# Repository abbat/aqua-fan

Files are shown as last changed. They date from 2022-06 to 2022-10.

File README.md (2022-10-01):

# aqua-fan

Проект кулера (вентиляторного охлаждения) для аквариума с крышкой. Позволяет понизить температуру воды в аквариуме на 4°C (±0.3°C) относительно комнатной, что актуально для помещений без кондиционера в летний период.

Изначально разрабатывался для аквариума [EHEIM vivalineLED 126](https://eheim.com/en_GB/aquatics/aquariums/aquariums-fresh-water/vivalineled/vivalineled-126), но это ограничение касается только модели корпуса для печати на 3D принтере (в программно-аппаратную же часть заложено масштабирование на различные конфигурации).

<p align='center'>
EHEIM vivaline aquarium fan cooler Вентиляторный кулер для аквариума EHEIM vivaline 126
EHEIM vivaline aquarium fan cooler Вентиляторный кулер для аквариума EHEIM vivaline 126
</p>

## Возможности

* Крепление на короб (крышку). Все коммерческие решения (например [GHL Aquarium Fans](https://www.aquariumcomputer.com/products/ghl-cooling-technology/aquarium-fans-propellerbreeze/), [Aqua Medic Arctic Breeze](https://www.aqua-medic.de/index.php?r=catalog/product&id=66&cid=34)) предполагают крепление блока вентиляторов клипсами на край стекла толщиной до 21 мм. Однако ширина короба аквариума данного типа 26 мм., что делает невозможным крепление на клипсы и потребовало бы открытия крышки (если бы крепление все же было возможно).
* Низкий уровень шума благодаря автоматической регулировке скорости вращения вентиляторов в зависимости от разницы температур (в отличии, например, от контроллеров [Aqua Medic Cool Control](https://www.aqua-medic.de/index.php?r=catalog/product&id=475&cid=34), у которых вентиляторы всегда работают на максимально разрешенной скорости).
* Контроль и подстройка скорости вращения по показаниям тахометров самих вентиляторов. Все коммерческие решения используют регулировку скорости вращения через изменение напряжения питания без использования обратной связи, а для различных моделей вентиляторов зависимость скорости вращения от напряжения может быть нелинейной (например см. спецификацию [be quiet! Pure Wings 2](https://www.bequiet.com/ru/casefans/505)) и разной даже для одной модели вентиляторов в блоке.

<p align='center'>
EHEIM vivaline aquarium fan cooler
EHEIM vivaline aquarium fan cooler
</p>

## Материалы

* [3D-модели](3d-model.md)
* [Аппаратное обеспечение](hardware.md)
* [Электрическая схема](schema.md)
* [Программное обеспечение](software.md)
* [Поддержка WiFi](wifi.md)

<p align='center'>
EHEIM vivaline aquarium fan cooler Вентиляторный кулер для аквариума с крышкой
EHEIM vivaline aquarium fan cooler Вентиляторный кулер для аквариума с крышкой
</p>

## Как можно помочь?

* Переведите этот документ или связанные материалы на свой родной язык;
* Исправляйте ошибки в этом документе или связанных материалах для своего родного языка;
* Делитесь информацией со своими друзьями;
* Отправляйте PR если вы имеете нестандартный аквариум под который не подходят коммерческие решения, разработчик, схемотехник или успешны в 3D моделировании и печати.

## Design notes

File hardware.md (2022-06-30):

# Аппаратное обеспечение

Все платы, датчики и расходники можно приобрести на AliExpress. Для упрощения поиска в описание добавлены ключевые слова и изображения.

ПО поддерживает от 1 до 3 вентиляторов с управлением скоростью вращения через `pwm` (4-pin). [Рекомендуется](fan-matrix.md) использовать вентиляторы `Noctua` - при хорошей производительности у них минимальный уровень шума (что особенно ценно в ночное время). Вообще, выбор хороших вентиляторов практически полностью определяет "удачность" конструкции - не экономьте на этом пункте.

<p align='center'>
Noctua NF-B9 redux-1600 PWM (92mm)
</p>

Так же, для уменьшения уровня шума, рекомендуется использовать силиконовые антивибрационные крепления, а для защиты лопастей вентиляторов - решетки. Для подключения вентиляторов используются коннекторы `KF2510-4AW`. Распайка коннекторов приведена в [схеме](schema.md), во время перепрограммирования плат(ы) вентиляторы должны отключаться от общей схемы!

<p align='center'>
Силиконовые крепления для вентиляторов
Металлические решетки для вентиляторов
4-pin коннкеторы KF2510-4AW для вентиляторов
</p>

В исходном проекте решетки крепятся силиконовыми креплениями непосредственно к вентиляторам, а сами вентиляторы удерживаются выступающей частью силиконовых креплений в специально отведенных внутренних пазах корпуса. Таким образом уменьшается передача вибрации от вентиляторов на корпус и далее на аквариум.

Для нестандартных вариантов крепления вентиляторов под крышкой могут помочь фиксирующие скобы ("пряжки") для объединения вентиляторов в блок, кронштейны для аквариумных светильников (например `NICREW`), поликарбонатные (акриловые) трубки (например `Uxcell`).

<p align='center'>
Фиксирующая скоба ("пряжка") для вентилятора
Кронштейны для аквариумных светильников NICREW
</p>

Контроллер вентиляторов работает на базе `Arduino Nano` или `Arduino Mini`. Рекомендуется `Arduino Nano`, т.к. для данной платы не потребуется дополнительно приобретать адаптер TTL (в случае его отсутствия). Так же подойдет любая другая плата `ATmega328` (`Arduino Uno`), но из за габаритов ее может не получится разместить в исходном корпусе.

При желании получения доступа по WiFi необходима дополнительная плата `Wi-Fi Wemos D1 Mini` (`ESP8266`). На практике данная возможность полезна только при активной разработке (перепрошивка через `OTA` без необходимости вскрытия корпуса и подключения к плате через USB). В обычной же жизни ("один раз настроил и забыл") эта возможность будет настолько редко востребованной, что усложнение схемы ради нее видится нецелесообразным.

В случае использования двух плат необходим блок питания на 5V. Для этих целей рекомендуется использовать `DC Power Shield for WEMOS D1 mini` (можно использовать любой другой блок питания, но с этим будет удобнее монтаж). В случае использования одноплатной схемы отдельный блок питания так же рекомендуется, но не является обязательным - `Arduino Nano` может быть напрямую запитана от 12V, а мощности ее внутреннего стабилизатора вполне достаточно для питания периферии.

<p align='center'>
Arduino Nano
Wi-Fi Wemos D1 Mini
DC Power Shield for WEMOS D1 mini
</p>

Питание в корпус подается через стандартный разъем 5.5 x 2.1 мм. от внешнего адаптера питания на 12V / 1A (одна плата) или 1.5А (две платы).

<p align='center'>
Разъем питания 5.5 x 2.1 мм.
Адаптер питания 12V / 2A (EU)
</p>

В качестве датчика температуры воды [рекомендуется](sensor-matrix.md) датчик `DS18B20` в пластиковом герметичном исполнении (ключевое слово для поиска `Taidacent DS18B20`).

<p align='center'>
Датчик температуры Taidacent DS18B20
Датчик температуры Sonoff DS18B20
</p>

Дополнительно для подключения датчика потребуются плата-адаптер с подтягивающим резистором, 4-pin разъем `PJ-392A` и 4-pin коннектор 3.5 мм. Разъем и коннектор опциональны, но с ними удобно отключать датчик при обслуживании. Распайка коннектора, совместимая с датчиками `Sonoff`, приведена в [схеме](schema.md).

<p align='center'>
Адаптер для подключения датчика температуры DS18B20
4-pin аудио разъем 3.5 мм.
4-pin аудио коннкетор 3.5 мм.
</p>

Дисплей `SSD1306 128x64` с интерфейсом IIC / I2C (4 pin, не путать с интерфейсом SPI - 7 pin). Данные дисплеи представлены в разных цветах (в том числе и с поддержкой двух цветов), рекомендуется использовать одноцветный голубой (не такой яркий ночью как желтый или белый). Наличие дисплея является опциональным, все необходимые параметры для работы ПО можно задать на этапе компиляции в файле конфигурации `config.h`.

<p align='center'>
Дисплей SSD1306 128x64 IIC/I2C
</p>

Сенсорные кнопки `TTP223` для конфигурирования температуры, ограничения мощности вентиляторов и других настроек. Кнопки имеют смысл только при наличии дисплея (т.е. так же являются опциональными). Сенсорные кнопки при отличной чувствительности через пластиковый корпус оказались и удобнее и дешевле механических.

<p align='center'>
Сенсорные кнопки TTP223
</p>

Зуммер ("пищалка") `KY-012` (активный, однотонный) или `KY-006` (пассивный, мелодии) - может использоваться для звуковой индикации ошибок или оповещения о событиях (ошибка вентиляторов, критическое повышение температуры и т.д.). На данный момент поддержка зуммеров не реализована в ПО, однако можно подключить пассивный зуммер с учетом возможных будущих доработок.

<p align='center'>
Зуммер ("пищалка") KY-012
Зуммер ("пищалка") KY-006
</p>

Для монтажа всех компонентов в корпусе потребуются провода типа `Dupont` (разноцветные), термоусадочные трубки (маленькие с учетом диаметра проводов), паяльник (припой, флюс), мультиметр, горячий клеевой пистолет, и прочие инструменты (кусачки, пинцет). Если вы не занимаетесь схемотехникой, то приобретать все это для разовой задачи не имеет смысла - для пайки десятка проводов будет дешевле обратиться к специалисту или в любой сервисный центр по ремонту техники.

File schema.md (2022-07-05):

# Электрическая схема

Контроллер может быть собран по двум схемам:

* На базе одной платы `Arduino Nano` (без поддержки WiFi)
* На базе двух плат `Arduino Nano` и `Wi-Fi Wemos D1 Mini` (с поддержкой WiFi)

Поддержка WiFi полезна только при активной разработке (перепрошивка через `OTA` без необходимости вскрытия корпуса и подключения к плате через USB). В обычной же жизни ("один раз настроил и забыл") эта возможность будет настолько редко востребованной, что усложнение схемы ради нее видится нецелесообразным.

Обе схемы отображают подключение коннекторов для 3-х вентиляторов. В случае использования меньшего количества вентиляторов можно просто убирать из схемы неиспользуемые (начиная с 3-го).

Обе схемы отображают подключение двух датчиков температуры воды:

* `DS18B20` (через адаптер и аудио-коннектор 3.5 мм.);
* Инфракрасный `GY-906` (`MLX90614`).

ПО может работать как с обоими датчиками одновременно, так и с любым из них. [Практические испытания](sensor-matrix.md) показали, что датчик `GY-906` достаточно сильно "шумит" из за внешних воздействий и, если вам не требуется дополнительный контроль по второму датчику, его можно исключить из схемы. Так же, если будет сделан выбор в пользу ИК-датчика `GY-906` (и неприемлемости погружения в воду `DS18B20` например, из соображений эстетики), можно исключить из схемы аудио-гнездо 3.5 mm и адаптер `DS18B20`.

Помимо датчика `GY-906` по шине I2C можно подключить любые дополнительные датчики по вашему усмотрению аналогично подключению `GY-906` (на данный момент эта возможность носит экспериментальный характер).

Дисплей `SSD1306 128x64` и сенсорные кнопки `TTP223` являются опциональными - все параметры ПО можно задать на этапе компиляции. Если вам не требуется визуальное отображение информации или не требуется изменение настроек (конфигурирования температуры, ограничения мощности вентиляторов и т.д.), то дисплей и / или кнопки можно исключить из схемы.

Обе схемы отображают подключение зуммера ("пищалки") `KY-006` для звуковой сигнализации о различных событиях (ошибка вентиляторов, критическое повышение температуры и т.д.). На данный момент ПО не поддерживает эту возможность, однако не исключена поддержка в будущем. Зуммер так же можно исключить из схемы.

Крепление плат в [корпусе](3d-model.md) производится на термоклей (поскольку отпечатать на 3D-принтере ровные аккуратные крепления не представляется возможным), монтаж навесной проводами типа `dupont` (для цветовой маркировки и / или возможности размыкания узлов). В случае необходимости демонтажа для термоклея можно использовать изопропиловый спирт.

## Схема 1

Схема с одной платой без поддержки WiFi.

<p align='center'>
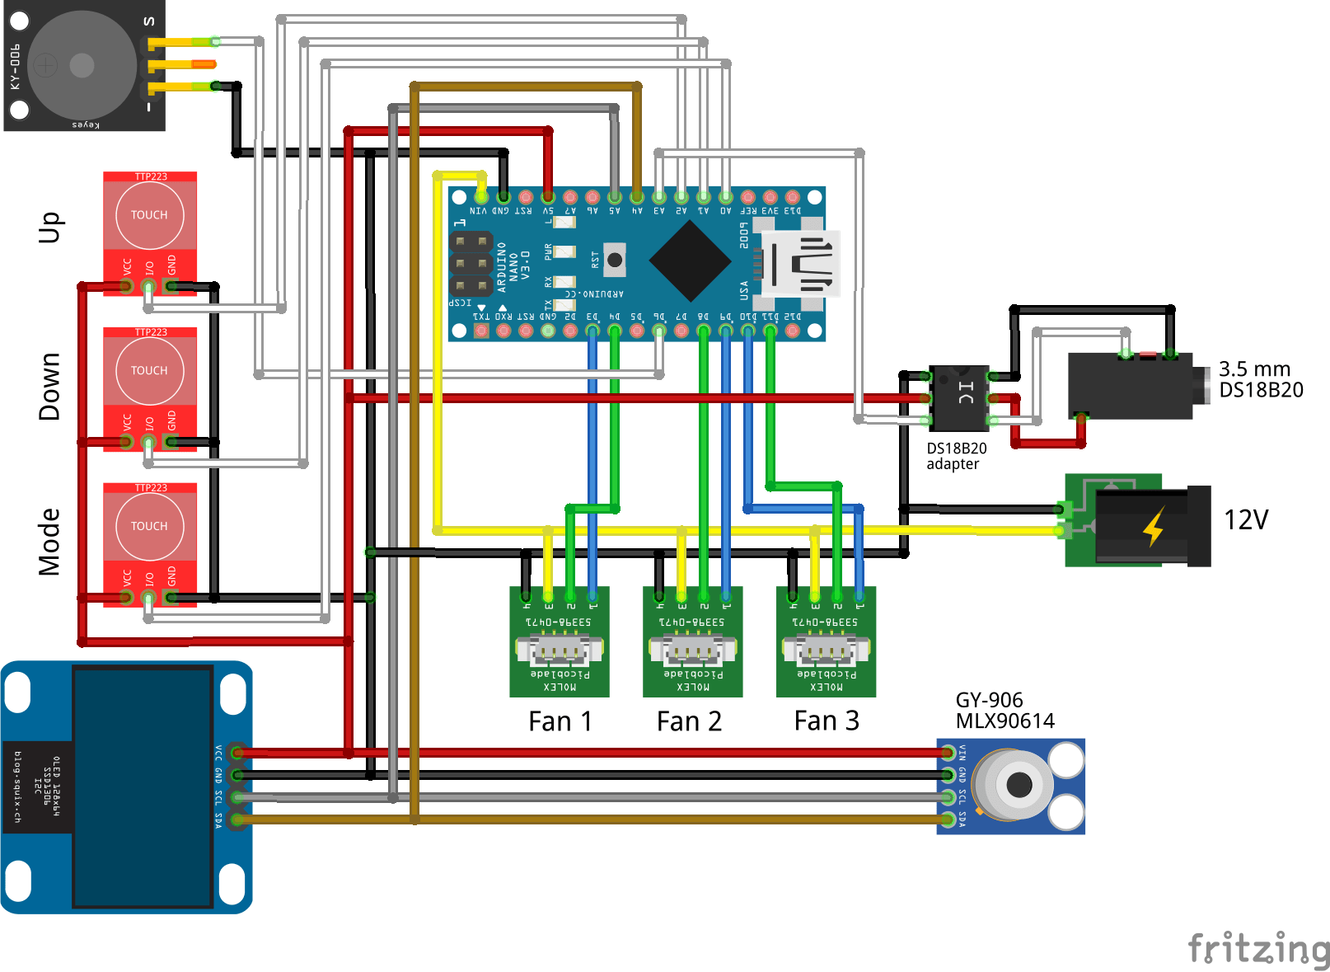
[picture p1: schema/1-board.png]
Одноплатная схема кулера для аквариума

</p>

## Схема 2

Схема с двумя платами и поддержкой WiFi.

<p align='center'>
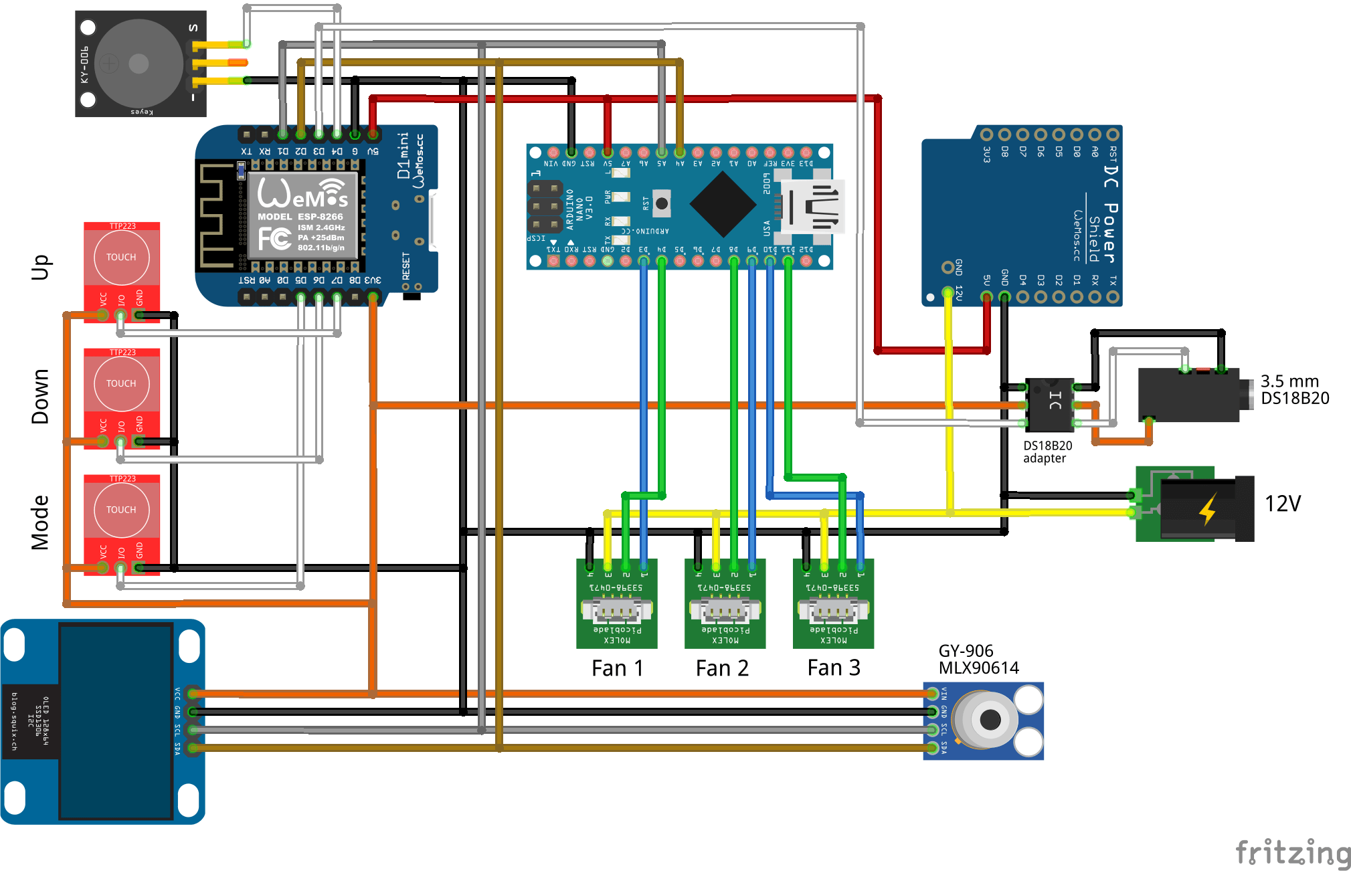
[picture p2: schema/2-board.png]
Схема кулера для аквариума с поддержкой WiFi

</p>

## Прочее

### DS18B20

При использовании датчика `DS18B20` аудио-штекер 3.5 мм. рекомендуется распаивать совместимым с датчиком `Sonoff` (который поставляется с уже распаяным штекером).

<p align='center'>
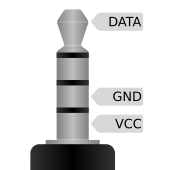
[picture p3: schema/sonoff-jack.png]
Распайка штекера Sonoff DS18B20

</p>

* `DATA` - данные (белый)
* `GND` - земля (черный)
* `VCC` - питание (красный +5V, оранжевый +3V, у датчика `Taidacent` - розовый)

При монтаже гнездо и штекер имеет смысл прозвонить мультиметром на соответствие контактов.

### KF2510-4AW

Штекер `KF2510-4AW` имеет ключ для корректного подключения вентилятора. Распайка штекера и гнезда приведена ниже:

<p align='center'>
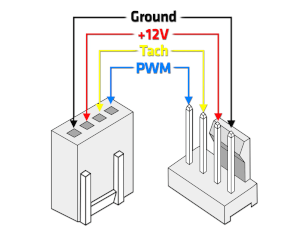
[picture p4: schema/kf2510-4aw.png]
Распайка штекера KF2510-4AW.png Распайка штекера KF2510-4AW

</p>

* `Ground` - земля (черный)
* `+12V` - питание (на схеме желтый)
* `Tach` - показания тахометра (на схеме зеленый)
* `PWM` - управление скоростью вращения (голубой)

## Как можно помочь?

Схемы созданы с использованием [fritzing.app](https://github.com/fritzing/fritzing-app), исходники лежат в директории `schema` проекта:

* [1-board.fzz](schema/1-board.fzz) - схема 1 (одна плата)
* [2-board.fzz](schema/2-board.fzz) - схема 2 (две платы)

Поскольку я делал это первый раз в жизни (как и держал пяльник), буду рад вашим PR с улчшениями.

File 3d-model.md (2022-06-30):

# 3D-модели

На текущий момент в проекте присутствует только одна модель корпуса для печати на 3D-принтере.

## EHEIM vivalineLED 126

### 3 x 92 мм. вентиляторы

<p align='center'>
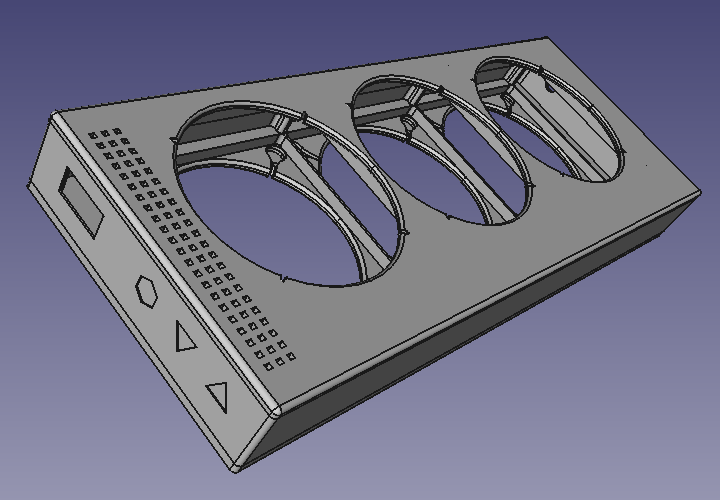
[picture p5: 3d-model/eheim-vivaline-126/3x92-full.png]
3D модель корпуса для EHEIM vivalineLED 126 и 3 x 92 мм. вентиляторов

</p>

Исходники модели в формате `FreeCAD` лежат в директории `3d-model/eheim-vivaline-126` проекта ([3x92-full.FCStd.xz](3d-model/eheim-vivaline-126/3x92-full.FCStd.xz)). Там же находятся готовые к печати `stl` файлы:

* [3x92-bottom.stl.xz](3d-model/eheim-vivaline-126/3x92-bottom.stl.xz) - низ корпуса, подоходит для всех вариантов верха;
* [3x92-top-power.stl.xz](3d-model/eheim-vivaline-126/3x92-top-power.stl.xz) - верх корпуса с единственным отверстием под гнездо питания, может использоваться если у вас уже есть внешний контроллер и не хватает только блока вентиляторов;
* [3x92-top-ds18b20.stl.xz](3d-model/eheim-vivaline-126/3x92-top-ds18b20.stl.xz) - верх корпуса с отверстием под аудио-гнездо 3.5 мм. датчика `DS18B20`, может использоваться если вам не требуется индикация параметров работы на дисплее;
* [3x92-top-display.stl.xz](3d-model/eheim-vivaline-126/3x92-top-display.stl.xz) - верх корпуса с дисплеем, может использоваться если вам нужна индикация работы, но не требуется настройка парамеров;
* [3x92-top-buttons.stl.xz](3d-model/eheim-vivaline-126/3x92-top-buttons.stl.xz) - верх корпуса с кнопками, наиболее полный вариант.

Объем модели (`FreeCAD.ActiveDocument.ActiveObject.Shape.Volume / 1000`) составляет приблизительно 305 см³. Отпечатана в типографии [replica-3d.ru](https://replica-3d.ru) без склеек.

## Как можно помочь?

Буду рад вашим PR с новыми моделями корпусов под другие типы аквариумов или количество вентиляторов.

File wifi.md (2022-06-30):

# Поддержка WiFi

На данный момент ПО поддерживает минимальный набор JSON-API. Запросы делаются по протоколу http.

## Получение статуса

**Запрос**:

`GET /status`

**Ответ**:

`HTTP-200` и JSON, или код ошибки с описанием.

```
{
   "uptime" : 274043,               # время в секундах с момента загрузки контроллера
   "fans" : {
      "speed" : 23.7456446,         # текущая скорость вентиляторов в процентах (усредненная)
      "uptime" : 64031,             # время в секундах с момента запуска вентиляторов
      "items" : [                   # статистика по каждому из вентиляторов
         {
            "hirpm" : 1896,         # максимальный rpm вентилятора
            "rpm" : 449,            # текущий rpm вентилятора
            "speed" : 23.6814346,   # текущая скорость вентилятора в процентах
            "base" : 454,           # требуемый rpm вентилятора от системы управления
            "lopwm" : 13,           # значение скважности pwm ниже которого вентилятор останавливается (0 - 255)
            "hipwm" : 23,           # значение скважности pwm выше которого вентилятор запускается (0 - 255)
            "pwm" : 56              # текущее значение скважности pwm (0 - 255)
         },
         ...
      ]
   },
   "sensors" : [                     # статистика по каждому из сенсоров
      {
         "filtered" : 24.38318063,   # текущее сглаженное значение температуры
         "value" : 24.35790526,      # текущее "сырое" значение температуры
         "type" : "water",           # датчик измерения температуры воды
         "role" : "secondary",       # роль датчика (вторичный)
         "unit" : "C",               # единица измерения (°C)
         "sensor" : "MLX90614"       # наименование датчика
      },
      {
         "value" : 27.74999428,
         "role" : "primary",         # роль датчика (первичный)
         "unit" : "C",
         "type" : "ambient",         # датчик измерения температуры воздуха
         "sensor" : "MLX90614"
      },
      ...
   ],
   "ips" : [                         # список IP адресов платы
      "192.168.1.XXX",
      "2a02:2168:XXXX:XXXX:XXXX:XXXX:XXXX:XXXX"
   ],
   "ts" : "2022-06-30T22:04:29Z"     # текущее время (UTC)
}
```

## Установка параметра

**Запрос**:

`POST /set`

**Параметры**:

* `water-temperature-base` - требуемое значение температуры в °C;
* `min-fan-speed` - минимальная скорость вентиляторов в процентах (0 - 100, не может быть больше `max-fan-speed`);
* `max-fan-speed` - максимальная скорость вентиляторов в процентах (0 - 100, не может быть меньше `min-fan-speed`);

**Ответ**:

`HTTP-200`, или код ошибки с описанием.

## Как можно помочь?

Буду рад вашим PR с расширением JSON-API и созданию полноценного веб-интерфейса управления.

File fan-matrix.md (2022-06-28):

# Выбор вентиляторов

Модель (производитель) вентиляторов выбирались исходя из [обзора](https://www.overclockers.ua/cooler/arctic-bequiet-enermax-noctua-thermalright-xigmatek-zalman-120mm/all/). Критерий - максимальная производительность при минимуме шума (~20dB/A - это уже достаточно шумно). Кандидаты:

* [Noctua](https://noctua.at/en/products/fan);
* [be quiet!](https://www.bequiet.com/en/casefans).

Ограничения по габаритам:

* Глубина корпуса: 318.2 мм. (для [EHEIM vivalineLED 126](https://eheim.com/en_GB/aquatics/aquariums/aquariums-fresh-water/vivalineled/vivalineled-126));
* Перегородка между вентиляторами: 1.2 мм. (стандартный диаметр сопла 3D-принтера составляет 0.4 мм., а толщина стенки рекомендуется минимум в 3 раза больше).

Прочие ограничения:

* Питание 12V (можно 5V, но они обычно более шумные);
* Одна плата arduino nano может управлять тремя pwm вентиляторами.

Сводная таблица представлена ниже, исключены заведомо проигрышные варианты по шуму или производительности, указана минимальная цена в рублях на момент написания (текущие цены могут существенно отличаться).

```
+------------------------+---------+------+------+-------+-------+
|          name          |  size   | rpm  | dB/A | m³/h  | price |
+------------------------+---------+------+------+-------+-------+
| NF-P14s redux-1200 PWM | 2 x 140 | 1200 | 19.6 | 220.6 |  2906 |
| NF-S12A PWM            | 2 x 120 | 1200 | 17.8 | 215.0 |  3260 |
| NF-S12B redux-1200 PWM | 2 x 120 | 1200 | 18.1 | 201.2 |  2396 |
| NF-B9 redux-1600 PWM   | 3 x  92 | 1600 | 17.6 | 192.9 |  2751 |
+------------------------+---------+------+------+-------+-------+
| Silent Wings 3-140     | 2 x 140 | 1000 | 15.5 | 202.2 |  3462 |
| Silent Wings 3-120     | 2 x 120 | 1450 | 16.4 | 171.6 |  3196 |
+------------------------+---------+------+------+-------+-------+
| Pure Wings 2-140       | 2 x 140 | 1000 | 18.8 | 208.0 |  1578 |
| Pure Wings 2-92        | 3 x  92 | 1900 | 19.6 | 168.0 |  1920 |
+------------------------+---------+------+------+-------+-------+
```

Особенностью вентиляторов `be quiet!` серии `Pure Wings` является то, что они [не останавливаются](https://www.bequiet.com/ru/casefans/618) при нулевой скважности pwm - т.е. регулирование скорости вращения возможно только по питанию и в [ограниченном диапазоне скоростей](https://www.bequiet.com/ru/casefans/505).

Итоговый выбор сводится к вариантам на базе `Noctua`:

* 2 x `NF-S12A PWM` / `NF-S12B redux-1200 PWM` - по 37.3 мм спереди и сзади по глубине под гнезда и дисплей;
* 3 x `NF-B9 redux-1600 PWM` - по 18.7 мм спереди и сзади по глубине под гнезда и дисплей.

Достоинства и недостатки 2-х вентиляторной схемы:

* `+` на 4 провода меньше;
* `+` больше пространства спереди и сзади под гнезда и платы;
* `-` корпус шире на 28 mm (возможно за счет перекомпановки это можно нивелировать);
* `-` меньше возможности по регулированию rpm на малых оборотах (когда часть вентиляторов может быть вообще выключена), но целесообразность этой возможности сомнительна.

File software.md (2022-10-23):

# Программное обеспечение

Исходный код находится в директории `src` проекта. Для сборки используется среда [Arduino IDE](https://www.arduino.cc/en/software) со следующими дополнительными библиотеками:

* [SoftTimers](https://github.com/end2endzone/SoftTimers);
* [GyverOLED](https://github.com/GyverLibs/GyverOLED);
* [GyverPWM](https://github.com/GyverLibs/GyverPWM);
* [EnableInterrupt](https://github.com/GreyGnome/EnableInterrupt).

Для работы с датчиками температуры используются следующие библиотеки:

* [OneWire](https://www.pjrc.com/teensy/td_libs_OneWire.html) - `DS18B20`;
* [DallasTemperature](https://github.com/milesburton/Arduino-Temperature-Control-Library) - `DS18B20`;
* [Adafruit-MLX90614-Library](https://github.com/adafruit/Adafruit-MLX90614-Library) - `GY-906` (`MLX90614ESF`).

Для работы в [схеме с двумя платами](schema.md) и поддержкой WiFi используются следующие библиотеки:

* [ESP8266 Arduino](https://arduino-esp8266.readthedocs.io/en/latest/);
* [ArduinoJSON](https://arduinojson.org/v6/api/).

Для работы с внешними (экспериментальными) датчиками используются следующие библиотеки:

* [Adafruit BME280 Library](https://github.com/adafruit/Adafruit_BME280_Library) - `BME280`;
* [arduino-sht](https://github.com/Sensirion/arduino-sht) - `SHT-3X` (`SHT-30`, `SHT-31`, `SHT-35`, `SHT-85`);
* [BH1750](https://github.com/claws/BH1750) - `BH1750`.

Все эти библиотеки могут быть установлены через менеджер библиотек `Arduino IDE`.

## Конфигурация

Конфигурация ПО задается в файле [config.h](src/config.h) через `#define` опции:

* `DISPLAY_TYPE` - тип дисплея:
  * (не задано) - система собирается и работает без поддержки дисплея и кнопок;
  * `DISPLAY_SSD1306_128_64` - поддержка дисплея `SSD1306 128x64` (включено по умолчанию в `config.h`).
* `PRIMARY_WATER_TEMPERATURE_SENSOR` - тип первичного (основного) датчика температуры воды:
  * `WATER_TEMPERATURE_SENSOR_DS18B20` - `DS18B20` (включено по умолчанию в `config.h`);
  * `WATER_TEMPERATURE_SENSOR_MLX90614` - `GY-906` (`MLX90614ESF`).
* `SECONDARY_WATER_TEMPERATURE_SENSOR` - типы вторичного (дополнительного) датчика температуры воды:
  * (не задано) - вторичный датчик отсутствует (по умолчанию);
  * остальные возможные значения такие же как у `PRIMARY_WATER_TEMPERATURE_SENSOR`.
* `ENABLE_WIFI` - включение [схемы с поддержкой WiFi](schema.md) (по умолчанию не задано):
  * `WIFI_SSID` - имя `SSID` для подключения к WiFi сети (по умолчанию не задано);
  * `WIFI_PASSWORD` - пароль для подключения к WiFi сети (по умолчанию не задано).

Экспериментальные опции:

* `EXTERNAL_SENSOR_0`, `EXTERNAL_SENSOR_1`, `EXTERNAL_SENSOR_2` - внешние сенсоры (по умолчанию не заданы):
  * `EXTERNAL_SENSOR_BME280` - датчик `BME280` (температура, влажность, давление);
  * `EXTERNAL_SENSOR_SHT3X` - датчик `SHT-3X` (температура, влажность).

### Контроллер

Значения ниже не используются, если они были сконфигурированы и сохранены в `EEPROM` (кнопками).

* `DEFAULT_WATER_TEMPERATURE_BASE` - базовая температура воды для поддержания в °C (по умолчанию 25);
* `DEFAULT_MIN_FAN_SPEED` - минимально разрешенная скорость вентиляторов в процентах (по умолчанию 0);
* `DEFAULT_MAX_FAN_SPEED` - максимально разрешенная скорость вентиляторов в процентах (по умолчанию 80).

Значения ниже не рекомендуются к изменению:

* `FAN_SPEED_TEMPERATURE_WINDOW` - ширина окна температур в °C в котором скорость вентиляторов меняется от 0 до 100% (по умолчанию 0.5);
* `WATER_TEMPERATURE_SENSOR_NOISE` - шум датчика в °C (по умолчанию 0.1 для `DS18B20` и 0.3 для `MLX90614`);
* `WATER_TEMPERATURE_SENSOR_NOISE_UPPER` - шум датчика в °C в сторону завышения показаний температуры (по умолчанию `WATER_TEMPERATURE_SENSOR_NOISE`);
* `WATER_TEMPERATURE_SENSOR_NOISE_LOWER` - шум датчика в °C в сторону занижения показаний температуры (по умолчанию `WATER_TEMPERATURE_SENSOR_NOISE`);
* `FAN_SPEED_NOISE_MULTIPLER` - основание логарифма для модели изменения скорости вращения вентиляторов (по умолчанию не задано - используется линейная модель, эквивалентная `FAN_SPEED_NOISE_MULTIPLER = 1`). Динамика изменения скорости вращения вентиляторов в зависимости от значения и разницы температур изображена на диаграме ниже. Значения более единицы подходят для очень тихих вентиляторов и удержания температуры в узком диапазоне. Значения менее единицы могут использоваться для шумных вентиляторов, но тогда придется пожертвовать диапазоном регулирования. На экспериментальном стенде стандартная линейная модель показала себя вполне адекватно и установка данной переменной в обычных условиях не требуется.

<p align='center'>
Зависимость изменения скорости работы вентиляторов от разницы температуры и FAN_SPEED_NOISE_MULTIPLER
</p>

* `FAN_SPEED_NOISE_HUMIDITY` - динамическое определение значения `FAN_SPEED_NOISE_MULTIPLER` в зависимости от влажности воздуха (по умолчанию не задано), где 100% влажности соответствует значению основания 10, и основанию 0.1 при влажности менее 1%. При задании опции `FAN_SPEED_NOISE_HUMIDITY` значение опции `FAN_SPEED_NOISE_MULTIPLER` игнорируется. Для работы требуется дополнительный датчик с поддержкой измерения влажности воздуха.

Алгоритм управления вентиляторами:

* Вентиляторы стартуют, если температура повысилась до значения `DEFAULT_WATER_TEMPERATURE_BASE` + `WATER_TEMPERATURE_SENSOR_NOISE_UPPER`;
* Вентиляторы останавливаются, если температура понизилась до значения `DEFAULT_WATER_TEMPERATURE_BASE` - `WATER_TEMPERATURE_SENSOR_NOISE_LOWER`;
* Вентиляторы работают на 100% мощности при превышении температуры `DEFAULT_WATER_TEMPERATURE_BASE` + `FAN_SPEED_TEMPERATURE_WINDOW`;
* Вентиляторы меняют скорость работы от 0 до 100% в диапазоне температур остановки и максимальной мощности.

### Датчики

**Общие параметры**

Значения ниже не рекомендуются к изменению:

* `FAST_SENSOR_UPDATE_INTERVAL` - время обновления показаний для "быстрых" датчиков в ms (по умолчанию 1000 = 1s);
* `STANDARD_SENSOR_UPDATE_INTERVAL` - время обновления показаний для "стандартных" датчиков в ms (по умолчанию 3000 = 3s);
* `SLOW_SENSOR_UPDATE_INTERVAL` - время обновления показаний для "медленных" датчиков в ms (по умолчанию 15000 = 15s).

**DS18B20**

* `ONE_WIRE_PIN` - номер `OneWire` пина для датчика (значение по умолчанию зависит от типа [схемы](schema.md), нельзя использовать пины D0 и D8 для платы `ESP8266`);
* `DS18B20_WATER_TEMPERATURE_SENSOR_INDEX` - индекс датчика (по умолчанию 0);
* `DS18B20_WATER_TEMPERATURE_SHIFT` - поправка датчика в °C (по умолчанию 0).

Значения ниже не рекомендуются к изменению:

* `DS18B20_WATER_TEMPERATURE_FILTER` - коэффициент IIR фильтра (по умолчанию 22, что соответствует ~5 минутам для стабилизации показаний при интервале обновления раз в 3s значения `STANDARD_SENSOR_UPDATE_INTERVAL`).

**MLX90614**

* `MLX90614_WATER_TEMPERATURE_SHIFT` - поправка датчика температуры объекта в °C (по умолчанию 0);
* `MLX90614_AMBIENT_TEMPERATURE_SHIFT` - поправка датчика температуры окружающего воздуха в °C (по умолчанию 0).

Значения ниже не рекомендуются к изменению:

* `MLX90614_WATER_TEMPERATURE_FILTER` - коэффициент IIR фильтра (по умолчанию 65 что соответствует ~5 минутам для стабилизации показаний при интервале обновления раз в 1s значения `FAST_SENSOR_UPDATE_INTERVAL`);
* `MLX90614_WATER_TEMPERATURE_MAX_FAILS` - максимальное число попыток измерения температуры объекта, прежде чем датчик будет переведен в режим ошибки (по умолчанию `MLX90614_AMBIENT_TEMPERATURE_MAX_FAILS`);
* `MLX90614_AMBIENT_TEMPERATURE_MAX_FAILS` - максимальное число попыток измерения температуры окружающего воздуха, прежде чем датчик будет переведен в режим ошибки (по умолчанию 60000 / `FAST_SENSOR_UPDATE_INTERVAL` = 60 попыток или 1 минута).

**BME280**

* `BME280_AMBIENT_TEMPERATURE_SHIFT` - поправка датчика температуры окружающего воздуха в °C (по умолчанию 0);
* `BME280_HUMIDITY_SHIFT` - поправка датчика влажности окружающего воздуха в % (по умолчанию 0);
* `BME280_PRESSURE_SHIFT` - поправка датчика давления окружающего воздуха в Па (по умолчанию 0).

**SHT-3X**

* `SHT3X_AMBIENT_TEMPERATURE_SHIFT` - поправка датчика температуры окружающего воздуха в °C (по умолчанию 0);
* `SHT3X_HUMIDITY_SHIFT` - поправка датчика влажности окружающего воздуха в % (по умолчанию 0).

**BH1750**

* `BH1750_LIGHT_SHIFT` - поправка датчика освещения в Lx (по умолчанию 0).

### Вентиляторы

* `FAN_COUNT` - количество вентиляторов (от 1 до 3, по умолчанию 3).

Значения ниже не рекомендуются к изменению:

* `FAN0_TAC` - номер пина tac (тахометр) для 1-го вентилятора (по умолчанию 4);
* `FAN1_TAC` - номер пина tac (тахометр) для 2-го вентилятора (по умолчанию 8);
* `FAN2_TAC` - номер пина tac (тахометр) для 3-го вентилятора (по умолчанию 11);
* `FAN_PWM_FREQ` - несущая частота pwm, Hz (по умолчанию 25000 = 25kHz);
* `FAN_UPDATE_INTERVAL` - интервал снятия показаний тахометра в ms (по умолчанию 2000 = 2s);
* `FAN_I2C_ADDRESS` - I2C адрес slave платы управления вентиляторами в схеме с двумя платами.

Из за особенностей генерации pwm, номера pwm-пинов жестко фиксированы на 3, 9 и 10.

### Дисплей

Дисплей неактивен, если не задан `DISPLAY_TYPE`.

* `DISPLAY_ADDRESS` - I2C адрес дисплея (по умолчанию `0x3C`).

Значения ниже не рекомендуются к изменению:

* `DISPLAY_UPDATE_INTERVAL` - время обновления информации на дисплее в ms (по умолчанию 1000 = 1s).

### Кнопки

Кнопки неактивны, если не задан `DISPLAY_TYPE`.

* `BUTTON_MODE_PIN` - номер пина для кнопки выбора режима (значение по умолчанию зависит от типа [схемы](schema.md));
* `BUTTON_DOWN_PIN` - номер пина для кнопки "вниз" (значение по умолчанию зависит от типа [схемы](schema.md));
* `BUTTON_UP_PIN` - номер пина для кнопки "вверх" (значение по умолчанию зависит от типа [схемы](schema.md)).

## Сборка

* Перед загрузкой ПО на плату отключите вентиляторы из схемы;
* Соедините нужную плату с компьютером через USB;
* Откройте проект в `Arduino IDE` и выберете нужный тип платы;
* Скомпилируйте и загрузите проект.

В случае использования двух плат рекомендуемые параметры сборки для `Wi-Fi Wemos D1 Mini`:

<p align='center'>
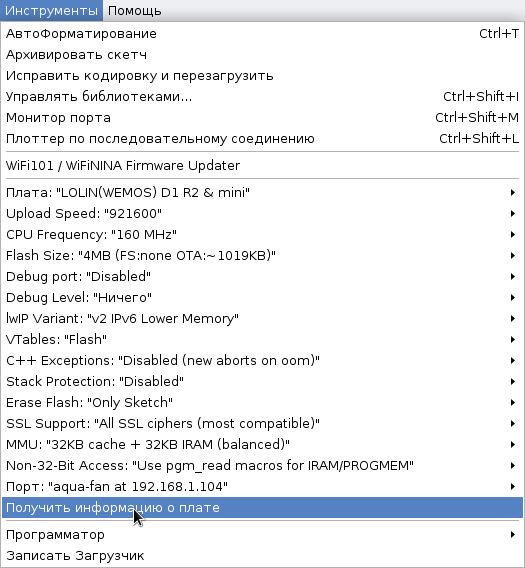
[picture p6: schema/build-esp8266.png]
Рекомендуемые параметры сборки для Wi-Fi Wemos D1 Mini

</p>

После первичной прошивки в дальнейшем можно использовать прошиву через `OTA` (по WiFi). Для этого может потребоваться разрешить на firewall компьютера трафик для `mDNS` и `OTA`. В терминах `iptables`:

```
# allow mdns
-A INPUT -d 224.0.0.251/32 -p udp -m udp --dport 5353 -j ACCEPT

# allow ota
-A INPUT -s 192.168.1.XXX/32 -p udp -j ACCEPT
-A INPUT -s 192.168.1.XXX/32 -p tcp -j ACCEPT
```

где `192.168.1.XXX` - адрес, назначенный WiFi плате.

## Как можно помочь?

Буду раз вашим PR с новыми функциями и исправлением ошибок.

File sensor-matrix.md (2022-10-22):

# Выбор датчиков

Критерий - удержание температуры воды без резких перепадов (например, 24°C ± 1°C в час). При этом по низкой стороне должен включаться обогреватель удерживающий температуру в нижнем диапазоне, а по высокой вентиляторы уже должны работать на 100% удерживая температуру в верхнем диапазоне. Поскольку одновременная работа обогревателя и вентиляторов является нецелесообразной, необходим диапазон температур, когда вентиляторы уже отключились, но нагреватель еще не включился и в обратную сторону. Поскольку большинство современных обогревателей (например, [EHEIM thermocontrol](https://eheim.com/en_GB/aquatics/technology/aquarium-heaters/thermocontrol-e/thermocontrol-e-100)) имеет точность ±0.5°C, то оптимальным режимом работы датчика будет 25°C ± 0.5°C.

Датчики с внешним креплением на стекло не рассматриваются по причине того, что при большой разнице температур (например, летом) им требуется хорошая теплоизоляция от внешней среды - корпус получится достаточно громоздким и не эстетичным.

Аналоговые датчики не рассматриваются по причине того, что в большинстве случаев они имеют более высокую погрешность и требуют самостоятельной упаковки в водонепроницаемую гильзу (т.е. дополнительный "колхоз").

Т.о. на рынке представлено по сути только два датчика для измерения температуры воды:

* `DS18B20` - погрешность ±0.5°C, разрешение 0.5°C - 0.0625°C (9-12 bit);
* `GY-906` (`MLX90614ESF-XXX`), разрешение 0.02°C:
  * `BAA` - погрешность ±0.5°C (single zone, 90° FOV);
  * `BCC` - погрешность ±0.5°C (gradient compensated, 35° FOV);
  * `DCI` - погрешность ±0.2°C (gradient compensated, 5° FOV).

## GY-906

Огромным достоинством датчика `GY-906` является то, что он не требует погружения в воду и может быть смонтирован прямо в корпусе с вентиляторами. Однако, точность показаний данного датчика очень сильно зависит от градиентов температур (подробности см. ["Thermal/Mechanical design recommendations - IR products"](https://www.melexis.com/en/documents/documentation/application-notes/application-note-thermal-mechanical-design-recommendations-ir-products)).

<p align='center'>
Инфракрасный датчик температуры GY-906 (MLX90614ESF)
</p>

На экспериментальном стенде возмущающими воздействиями на показания `GY-906` оказались:

* рябь на поверхности воды от флейты фильтра и свободно плавающие растения;
* излучение LED ламп под крышкой;
* градиенты температур и сильная рябь на поверхности воды при включенных вентиляторах.

Диаметр измеряемого пятна на расстоянии датчика в 5 см. от поверхности воды:

* `BAA` (90° FOV) ~ 10.0 см.;
* `BCC` (35° FOV) ~ 3.15 см.;
* `DCI` (5° FOV)  ~ 0.43 см.

Все датчики в разной степени будут захватывать отраженное тепло LED-ламп, которые находятся на расстоянии приблизительно 3 см. от зеркала воды и имеют угол рассеивания в 120° (+5.2 см. по габариту лампы).

Средняя и стандартная ошибки показаний откалиброванного датчика `DCI` (5° FOV) относительно `DS18B20` (взятого за эталон) на экспериментальном стенде за три месяца наблюдений (июль-сентябрь, ~400 тыс. значений) в различных условиях составляет:

* в идеальных условиях без ламп и вентиляторов: Δ = -0.05°C, σ = 0.12 (±0.36°C) - средняя ошибка меньше разрешения датчика `GY-906`;
* с лампами, но без вентиляторов: Δ = +0.59°C, σ = 0.10 (±0.30°C) - датчик `GY-906` завышает показания т.к. захватывает отраженное тепло LED-ламп.

Если посмотреть на распределение частот ошибки, то явно видно два пика при работающих и отключенных лампах:

<p align='center'>
Ошибка показаний датчика MLX90614ESF относительно DS18B20 с включенными и отключенными лампами
</p>

Третий левый пик в распределении частот ошибок наблюдался в сентябрьское межсезонье при температуре окружающего воздуха ниже базовой для аквариума, включенном нагревателе и очень высокой (более 50%) относительной влажности. С включением центрального отопления распределение ошибки вернулось к обычным значениям.

С работающими вентиляторами LED-лампы уже не оказывают значимого влияния на ошибку: Δ = -0.19°C, σ = 0.20 (±0.6°C) - при работающих вентиляторах зеркало воды охлаждается потоком воздуха и датчик `GY-906` занижает показания.

<p align='center'>
Ошибка показаний датчика MLX90614ESF относительно DS18B20 с включенными вентиляторами
</p>

Так же представляет интерес динамика изменения ошибки во время переходного процесса после включения вентиляторов:

<p align='center'>
Изменение ошибки показаний датчика MLX90614ESF относительно DS18B20 после включения вентиляторов
</p>

Корпус датчика охлаждается медленнее (и неравномерно) в сравнении с зеркалом воды сразу после начала движения воздуха. В результате изменения градиентов температур наблюдается мгновенное изменение "сырого" значения ошибки, которое впоследствии догонит фильтр, призванный сглаживать шум показаний от ряби на поверхности воды и проплывающих под датчиком растений.

Аналогичные переходные процессы можно наблюдать и в момент остановки вентиляторов, только в зависимости от состояния LED-ламп мгновенное изменение сырого значения температуры будет отличаться на ошибку измерения отраженного тепла - от +0.2°C при отключенных лампах до +0.8°C при включенных (см. выше).

Ошибка на всем интервале наблюдений на экспериментальном стенде составляет: Δ = -0.07°C, σ = 0.29 (±0.87°C). На практике это означает, что при базовой температуре в аквариуме в 25°C реальная температура будет поддерживаться в диапазоне от 23°C (точка включения нагревателя 23.5°C с погрешностью ±0.5°C) до 26°C.

**Вывод**: использование датчика `GY-906` имеет смысл только из эстетических соображений. По всем остальным параметрам он уступает датчику `DS18B20`.

## DS18B20

Недорогой, хорошо зарекомендовавший себя датчик. Может продаваться как в металлических, так и в пластиковых гильзах (в исполнении `Sonoff` так же комплектуется 4-pin 3.5 мм. штекером). По некоторым отзывам металлические гильзы в воде быстро деградируют, да и выглядят менее эстетично нежели пластиковые. При этом исполнение в пластиковой гильзе тяжелее найти (возможное ключевое слово `Taidacent`) и они сильно дороже.

<p align='center'>
Датчик температуры Taidacent DS18B20
Датчик температуры Sonoff DS18B20
</p>

[Калибровку датчика](https://www.kandrsmith.org/RJS/Misc/Thermometers/absolute_ds18b20.html) в домашних условиях можно провести по "тройной точке воды". Процедура приготовления "ледяной ванны" с погрешностью ±0.002°C подробно описана в [NIST Technical Note 1411, 'Reproducibility of the temperature of the ice point in routine measurements'](https://nvlpubs.nist.gov/nistpubs/Legacy/TN/nbstechnicalnote1411.pdf).

## Прочие

Скорость испарения воды в водоеме (а значит и понижение температуры) зависит от скорости ветра, влажности, разности температур, давления. С описанием различных моделей можно ознакомиться в "A critical review on equations employed for the calculation of the evaporation rate from free water surfaces", Ernani Sartori (журнал Solar Energy, Volume 68, Issue 1, January 2000, Pages 77-89).

Однако, данные модели используются на больших водоемах и интервалах времени. В условиях аквариума и суточных колебаний температур единственным статистически значимым фактором, влияющим на скорость изменения температуры воды, является скорость потока воздуха (обороты вентиляторов).

Дополнительно, поскольку корпус вентиляторов устанавливается на границе раздела сред (комнатной температуры и температуры воды в аквариуме, комнатной влажности и практически 100% влажности под крышкой), датчики внутри корпуса будут показывать некоторые промежуточные значения в зависимости от работы вентиляторов.

Т.о. использование дополнительных датчиков (влажности, температуры воздуха, давления) в качестве источника дополнительной информации для регулирования скорости работы вентиляторов является нецелесообразным (а при монтаже внутри корпуса вентиляторов еще и сложно интерпретируемым).

Тем не менее ПО поддерживает использование дополнительных внешних датчиков температуры, влажности, давления и освещения (см. [Программное обеспечение](software.md)).

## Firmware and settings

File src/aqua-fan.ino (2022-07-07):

#include "fan.h"
//----------------------------------------------------------------------------------------------
#ifndef AQUA_FAN_SLAVE
  #include "wifi.h"
  #include "button.h"
  #include "sensor.h"
  #include "eeprom.h"
  #include "display.h"
  #include "controller.h"
#endif   // !AQUA_FAN_SLAVE
//----------------------------------------------------------------------------------------------

void setup() {
  // must be first
  if (fanSetup() == false) {
    // TODO: beep error!!!
  }

#ifndef AQUA_FAN_SLAVE
  #ifdef DISPLAY_TYPE
    if (displaySetup() == false) {
      // TODO: beep error!!!
    }
  #endif

  if (sensorSetup() == false) {
    // TODO: display error!!!
  }

  if (eepromSetup() == false) {
    // TODO: display error!!!
  }

  // init controller
  if (controllerSetup() == false) {
    // TODO: display error!!!
  }

  #ifdef DISPLAY_TYPE
    if (buttonSetup() == false) {
      // TODO: beep error!!!
    }
  #endif
#endif   // !AQUA_FAN_SLAVE

#ifdef AQUA_FAN_MASTER
  if (wifiSetup() == false) {
    // TODO: display error!!!
  }
#endif

#ifndef AQUA_FAN_SLAVE
  #ifdef DISPLAY_TYPE
    displayClear();
  #endif
#endif   // !AQUA_FAN_SLAVE
}
//----------------------------------------------------------------------------------------------

void loop() {
  fanLoop();

#ifndef AQUA_FAN_SLAVE
  sensorLoop();
  controllerLoop();

  #ifdef DISPLAY_TYPE
    buttonLoop();
    displayLoop();
  #endif
#endif   // !AQUA_FAN_SLAVE

#ifdef AQUA_FAN_MASTER
  wifiLoop();
#endif
}
//----------------------------------------------------------------------------------------------

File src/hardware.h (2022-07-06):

#ifndef _AQUA_FAN_HARDWARE_H_
#define _AQUA_FAN_HARDWARE_H_

//----------------------------------------------------------------------------------------------
// display types
//----------------------------------------------------------------------------------------------

#define DISPLAY_SSD1306_128_64 0x01
#define DISPLAY_SSD1306_128_32 0x02

//----------------------------------------------------------------------------------------------
// water temperature sensor types
//----------------------------------------------------------------------------------------------

// Dallas Semiconductor / Maxim Integrated
#define WATER_TEMPERATURE_SENSOR_DS18B20    0x01   /* ±0.50°C */

// Melexis
#define WATER_TEMPERATURE_SENSOR_MLX90614   0x11   /* ±0.50°C / ±0.20°C */

//----------------------------------------------------------------------------------------------
// external sensor types (experimental)
//----------------------------------------------------------------------------------------------

// Microchip
#define EXTERNAL_SENSOR_MCP9808             0x21   /* ±0.25°C */

// Aosong Electronics Co.,Ltd / ASAIR
#define EXTERNAL_SENSOR_AHT10               0x31   /* ±0.30°C / ±2.0% Rh */
#define EXTERNAL_SENSOR_AHT15               0x32   /* ±0.30°C / ±2.0% Rh */
#define EXTERNAL_SENSOR_AHT20               0x33   /* ±0.30°C / ±2.0% Rh */

// Measurement Specialties / MEAS
#define EXTERNAL_SENSOR_HTU21               0x41   /* ±0.30°C / ±3.0% Rh */
#define EXTERNAL_SENSOR_HTU31               0x42   /* ±0.20°C / ±2.0% Rh */

// Texas Instruments
#define EXTERNAL_SENSOR_HDC1080             0x51   /* ±0.20°C / ±2.0% Rh */
#define EXTERNAL_SENSOR_HDC2080             0x52   /* ±0.20°C / ±2.0% Rh */

// Sensirion
#define EXTERNAL_SENSOR_SHT20               0x61   /* ±0.50°C / ±3.0% Rh */
#define EXTERNAL_SENSOR_SHT21               0x62   /* ±0.30°C / ±2.0% Rh */
#define EXTERNAL_SENSOR_SHT3X               0x63
#define EXTERNAL_SENSOR_SHT30               EXTERNAL_SENSOR_SHT3X   /* ±0.20°C / ±2.0% Rh */
#define EXTERNAL_SENSOR_SHT31               EXTERNAL_SENSOR_SHT3X   /* ±0.20°C / ±2.0% Rh */
#define EXTERNAL_SENSOR_SHT35               EXTERNAL_SENSOR_SHT3X   /* ±0.10°C / ±1.5% Rh */
#define EXTERNAL_SENSOR_SHT85               EXTERNAL_SENSOR_SHT3X   /* ±0.10°C / ±1.5% Rh */

// Bosch Sensortec
#define EXTERNAL_SENSOR_BMP180              0x71   /* ±0.50°C / ±1.0 hPA */
#define EXTERNAL_SENSOR_BMP280              0x72   /* ±0.50°C / ±1.0 hPA */
#define EXTERNAL_SENSOR_BME280              0x73   /* ±0.50°C / ±3.0% Rh / ±1.0 hPA */
#define EXTERNAL_SENSOR_BME680              0x74   /* ±0.50°C / ±3.0% Rh / ±0.6 hPA */

// GY-302
#define EXTERNAL_SENSOR_BH1750              0x81   /* ±1 Lx */

//----------------------------------------------------------------------------------------------
#endif   // _AQUA_FAN_HARDWARE_H_

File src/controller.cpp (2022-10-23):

#include "controller.h"
//----------------------------------------------------------------------------------------------
#ifndef AQUA_FAN_SLAVE
//----------------------------------------------------------------------------------------------
#include "fan.h"
#include "sensor.h"
#include "eeprom.h"
//----------------------------------------------------------------------------------------------
// https://github.com/end2endzone/SoftTimers
#include <SoftTimers.h>

#ifndef FAN_UPDATE_INTERVAL
  // fan update interval, ms
  // 2s is enougth for 95% rpm accuracy
  #define FAN_UPDATE_INTERVAL 2000
#endif

// timer for update fans
static SoftTimer fan_timer;

// last known fan speed, 1/%
static double fan_speed = 0;

#ifdef AQUA_FAN_MASTER
  // fan rotate start/stop time
  static unsigned long fan_uptime = 0;
#endif

// master or standalone fan status
typedef struct fan_s {
  byte pwm;     // current pwm
  byte lopwm;   // last known stop pwm
  byte hipwm;   // last known start pwm
  word rpm;     // last known rpm
  word hirpm;   // last known max rpm
  word base;    // required rpm
} fan_t;

static fan_t* fan       = NULL;
static byte   fan_count = 0;
//----------------------------------------------------------------------------------------------

void setPWM(byte i, byte pwm) {
  if (fan[i].pwm != pwm && fanPWM(i, pwm) == true) {
    fan[i].pwm = pwm;
  }
}
//----------------------------------------------------------------------------------------------

void updateRPM() {
  // recalibrate fans
  word srpm = 0;
  word hrpm = 0;
  for (byte i = 0; i < fan_count; i++) {
    word r = fan[i].rpm;
    fan[i].rpm = fanRPM(i);
    if (fan[i].rpm == (word)(-1)) {
        // error recovery
        fan[i].rpm = r;
        continue;
    }

    // change max fan rpm
    if (fan[i].hirpm < fan[i].rpm || fan[i].pwm == 255) {
      fan[i].hirpm = fan[i].rpm;
    }

    // if fan was in stopped state and rotated now, set new start pwm value
    if (r == 0 && fan[i].rpm > 0 && (fan[i].hipwm == 0 || fan[i].hipwm > fan[i].pwm)) {
      fan[i].hipwm = fan[i].pwm;
    }

    // if fan was in rotating state and stopped now, set new stop pwm value
    if (r > 0 && fan[i].rpm == 0 && fan[i].lopwm <= fan[i].pwm) {
      fan[i].lopwm = fan[i].pwm + 1;
    }

    srpm += fan[i].rpm;
    hrpm += fan[i].hirpm;
  }

  double fs;
  if (hrpm == 0) {
    fs = 0;
  } else {
    fs = (double)srpm / hrpm;
  }

  #ifdef AQUA_FAN_MASTER
    if ((fan_speed == 0 && fs != 0) || (fan_speed != 0 && fs == 0)) {
      fan_uptime = millis();
    }
  #endif

  fan_speed = fs;
}
//----------------------------------------------------------------------------------------------

void updateFans() {
  for (byte i = 0; i < fan_count; i++) {
    // if fan direction is to stop and it still not stopped, slow-down decrease rotation speed
    if (fan[i].base == 0) {
      if (fan[i].pwm != 0) {
        setPWM(i, fan[i].pwm - 1);
      }

      continue;
    }

    // 1 pwm ~ 7 rpm
    const word rpm_per_pwm = 7;

    // slow up / down speed to base rpm
    short dpwm;
    if (fan[i].rpm < fan[i].base && fan[i].base - fan[i].rpm > rpm_per_pwm) {
      if (fan[i].pwm == 0) {
        // start fan from stopped state
        dpwm = fan[i].hipwm;
      } else {
        dpwm = 1;
      }
    } else if (fan[i].rpm > fan[i].base && fan[i].rpm - fan[i].base > rpm_per_pwm) {
      dpwm = -1;
    } else {
      continue;
    }

    // new pwm
    short pwm = constrain(dpwm + fan[i].pwm, 0, 255);

    // disable stopping before reaching the temperature base
    if (pwm < fan[i].lopwm) {
      pwm = fan[i].lopwm;
    }

    setPWM(i, pwm);
  }
}
//----------------------------------------------------------------------------------------------
#if defined(FAN_SPEED_NOISE_MULTIPLER) || defined(FAN_SPEED_NOISE_HUMIDITY)
inline double log_base(double value, double base) {
  if (base == M_E) {
    return log(value);
  } else if (base == 10.0) {
    return log10(value);
  } else if (base == 1.0) {
    return value;
  } else if (base <= 0.0) {
    return 0.0;
  }

  return log(value) / log(base);
}
#endif   // FAN_SPEED_NOISE_MULTIPLER || FAN_SPEED_NOISE_HUMIDITY
//----------------------------------------------------------------------------------------------

void updateDirections()
{
  #ifndef WATER_TEMPERATURE_SENSOR_NOISE
    #if PRIMARY_WATER_TEMPERATURE_SENSOR == WATER_TEMPERATURE_SENSOR_MLX90614
      #define WATER_TEMPERATURE_SENSOR_NOISE 0.3
    #elif PRIMARY_WATER_TEMPERATURE_SENSOR == WATER_TEMPERATURE_SENSOR_DS18B20
      // 0.0625 * 1.5 = 0.09375 ~ 0.1
      #define WATER_TEMPERATURE_SENSOR_NOISE 0.1
    #else
      #error "Unsupported water temperature sensor"
    #endif
  #endif

  // lower bound of prescion hysteresis
  #ifndef WATER_TEMPERATURE_SENSOR_NOISE_LOWER
    #define WATER_TEMPERATURE_SENSOR_NOISE_LOWER WATER_TEMPERATURE_SENSOR_NOISE
  #endif

  // upper bound of prescion hysteresis
  #ifndef WATER_TEMPERATURE_SENSOR_NOISE_UPPER
    #define WATER_TEMPERATURE_SENSOR_NOISE_UPPER WATER_TEMPERATURE_SENSOR_NOISE
  #endif

  // temperature window for 0-100% of fan speed
  #ifndef FAN_SPEED_TEMPERATURE_WINDOW
    #define FAN_SPEED_TEMPERATURE_WINDOW 0.5
  #endif

  double water_temperature = primaryWaterTemperature();

  // actual and base water temperature diff
  double dt = water_temperature - waterTemperatureBase();
  if (dt <= -WATER_TEMPERATURE_SENSOR_NOISE_LOWER) {
    // current water temperature <= base water temperature - stop fans
    for (byte i = 0; i < fan_count; i++) {
      fan[i].base = 0;
    }
    return;
  } else if (dt <= WATER_TEMPERATURE_SENSOR_NOISE_UPPER && fan_speed == 0) {
    // disable fan start before prescion hysteresis excess
    return;
  }

  // fan speed model
  if (dt >= FAN_SPEED_TEMPERATURE_WINDOW) {
    // maximum speed if delta too high
    dt = 1.0;
  } else {
    // linear speed in temperature window
    dt = (dt + WATER_TEMPERATURE_SENSOR_NOISE_LOWER) / (FAN_SPEED_TEMPERATURE_WINDOW + WATER_TEMPERATURE_SENSOR_NOISE_LOWER);

    // logarithm speed in temperature window
    #if defined(FAN_SPEED_NOISE_HUMIDITY)
      double base = humidity();
      if (base == HUMIDITY_NULL_VALUE) {
        base = M_E;     // like ~27% humidity
      } else if (base < 1.0) {
        base = 0.1;     // like 1% humidity
      } else {
        base /= 10.0;   // map 1-100% humidity to 0.1-10 base
      }
      dt = log_base(dt * (base - 1.0) + 1.0, base);
    #elif defined(FAN_SPEED_NOISE_MULTIPLER)
      // FAN_SPEED_NOISE_MULTIPLER must be (0..1) for lower noise or (1..∞) for more agressive
      dt = log_base(dt * (FAN_SPEED_NOISE_MULTIPLER - 1.0) + 1.0, FAN_SPEED_NOISE_MULTIPLER);
    #endif
  }

  // limit rpm to range min/max fan speed
  const double max_fan_speed = maxFanSpeedF();
  if (dt > max_fan_speed) {
    dt = max_fan_speed;
  } else {
    const double min_fan_speed = minFanSpeedF();
    if (dt < min_fan_speed) {
      dt = min_fan_speed;
    }
  }
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

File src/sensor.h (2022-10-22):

#ifndef _AQUA_FAN_SENSOR_H_
#define _AQUA_FAN_SENSOR_H_
//----------------------------------------------------------------------------------------------
#include "aqua-fan.h"
//----------------------------------------------------------------------------------------------
#ifndef AQUA_FAN_SLAVE
//----------------------------------------------------------------------------------------------
// unknown / null ambient temperature, °C
#define AMBIENT_TEMPERATURE_NULL_VALUE -274
//----------------------------------------------------------------------------------------------
// unknown / null water temperature, °C
#define WATER_TEMPERATURE_NULL_VALUE -274
//----------------------------------------------------------------------------------------------
// unknown / null humidity, %
#define HUMIDITY_NULL_VALUE -1
//----------------------------------------------------------------------------------------------
// unknown / null pressure, hPa
#define PRESSURE_NULL_VALUE -1
// Pa in mm Hg
#define PRESSURE_PA_IN_MMHG 133.3223684
//----------------------------------------------------------------------------------------------
// unknown / null light, Lx
#define LIGHT_NULL_VALUE -1
//----------------------------------------------------------------------------------------------
bool sensorSetup();
void sensorLoop();
//----------------------------------------------------------------------------------------------
double primaryWaterTemperature();
//----------------------------------------------------------------------------------------------
bool   haveSecondaryWaterTemperature();
double secondaryWaterTemperature();
//----------------------------------------------------------------------------------------------
bool   haveAmbientTemperature();
double ambientTemperature();
//----------------------------------------------------------------------------------------------
bool   haveHumidity();
double humidity();
//----------------------------------------------------------------------------------------------
bool   havePressure();
double pressure();
//----------------------------------------------------------------------------------------------
bool   haveLight();
double light();
//----------------------------------------------------------------------------------------------
#ifdef AQUA_FAN_MASTER
  // https://arduinojson.org/v6/api/
  #include <ArduinoJson.h>

  void serializeSensors(JsonArray& json_sensors);
#endif   // AQUA_FAN_MASTER
//----------------------------------------------------------------------------------------------
#endif   // !AQUA_FAN_SLAVE
//----------------------------------------------------------------------------------------------
#endif   // _AQUA_FAN_SENSOR_H_

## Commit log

2022-06-27 README, возможности
2022-06-27 README, возможности (typo fix)
2022-06-28 fan matrix
2022-06-29 hardware boards & power
2022-06-29 hardware, sensor
2022-06-29 type sensor-matrix.md
2022-06-30 add fritzing schema
    [1-board.fzz, 2-board.fzz]
2022-07-05 external experimental sensors (BME280)
2022-07-06 Add SHT-3X external sensor
2022-07-11 refactoring fan recalibration
2022-10-01 Статистика по датчику MLX90614ESF
2022-10-20 Калибровка ds18b20 (ссылка)
2022-10-22 Отображение информации от внешних сенсоров
2022-10-22 Улучшение отображения информации от внешних сенсоров
2022-10-22 Экспериментальная модель FAN_SPEED_NOISE_HUMIDITY
2022-10-22 FAN_SPEED_NOISE_HUMIDITY sensor check
2022-10-22 Add BH1750 external sensor
